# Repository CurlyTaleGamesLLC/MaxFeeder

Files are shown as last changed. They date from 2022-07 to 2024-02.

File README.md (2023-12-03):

# Max Feeder

<video autoplay loop muted src="https://user-images.githubusercontent.com/25337335/216802715-1deb94b0-7a2f-4627-93f5-1e41935b5955.mp4">
</video>

## Part Feeding Simplified
### Designed to automate feeding parts for your Open PnP compatible pick and place machine
<br/>

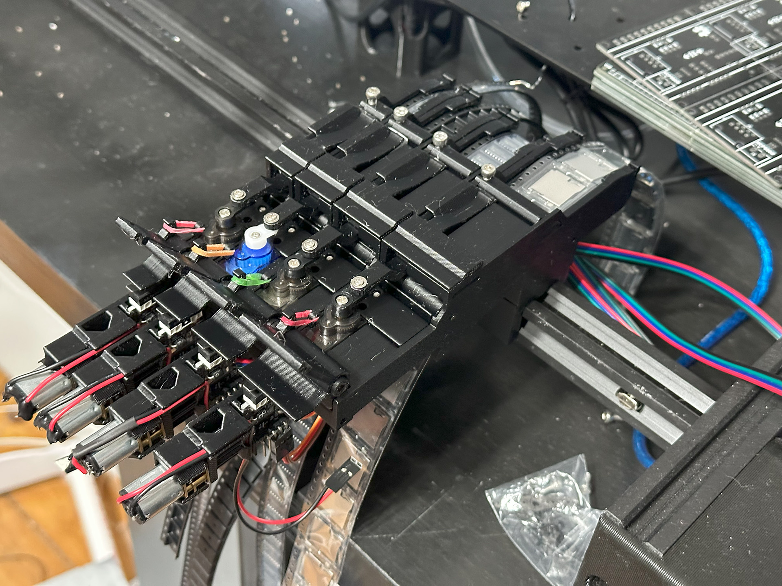
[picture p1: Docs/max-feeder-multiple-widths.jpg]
Max Feeders of multiple widths


This feeder is designed to be set up as an AutoFeeder in OpenPNP. It easily clips to 2020 aluminum extrusion and uses an Arduino Mega to receive Gcode commands sent over a USB serial connection in Open PnP. The Max Feeder Shield can control up to 34 feeders.

The design of the Max Feeder is based on [the 0816 feeder design from mgrl.](https://docs.mgrl.de/maschine:pickandplace:feeder:0816feeder) However after two years of development I redesigned every piece of it to improve and simplify the feeder as much as possible.

During development, I also referenced the remix of the 0816 feeder made Nicmoly for the Lumen PNP.

<br/>

# Where can I get a Max Feeder?

[I am selling kits of the Max Feeder Shield and kits of 5x 8mm Max Feeders.](https://store.curlytalegames.com/pages/max-feeders)
> The online store is now live! Thanks for supporting this open hardware project!

This is an Open Hardware project, so all of the design files and the BOM are included in this repo as well.

[If you like what I'm doing consider becoming a Github Sponsor :gift_heart:](https://github.com/sponsors/CurlyTaleGames)

<br/>

# Hardware

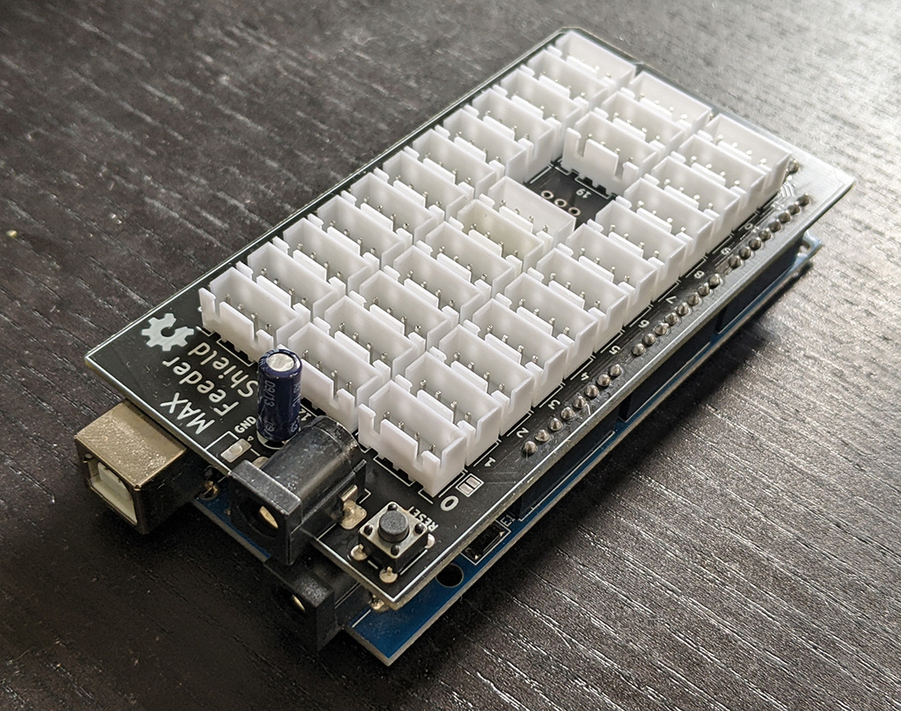
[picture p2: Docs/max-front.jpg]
Max Feeder Shield


## Max Feeder Shield
- 1 - Max Feeder Shield PCB
- 34 - 4 Pin 2.54mm JST connectors
- 1 - Arduino Mega
- 1 - 10uf Capacitor
- 1 - Barrel Jack
- 1 - 3.81mm Screw Terminal - Optional
- 1 - 6mm Through Hole Tacticle Switch
- 1 - 5v DC 3A (or more) Power Supply
- LOTS of 2.54mm Male Header
- Mounting Bracket in the "3D" folder

<br/>

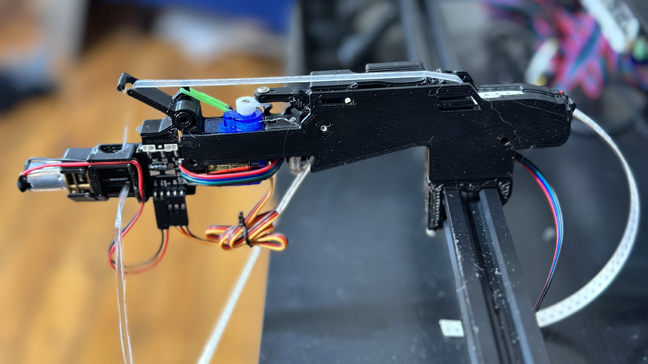
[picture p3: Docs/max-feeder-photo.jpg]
Max Feeder 8mm


## Max Feeder
- 1 - Max Feeder PCB
- 3D printed files in the "3D" folder
- 5 - [M3 6mm screws](https://www.amazon.com/Alloy-Steel-Socket-Screws-Black/dp/B00W8YSCIS/)
- 1 - [4 Pin 2.54mm JST cables 100cm in length ("stepper motor cable")](https://www.amazon.com/Wires-Motor-XH2-54-4P-PH2-0-6P-Printers-Accessories%EF%BC%8C3D/dp/B08PV6XGK2/)
- 3 - [M3 20mm screws](https://www.amazon.com/Prime-Line-9180478-Socket-Screws-10-Pack/dp/B07D5S3154/)
- 1 - [SPDT Limit Switch](https://www.amazon.com/dp/B088W8WMTB)
- 1 - [1N4001 Diode](https://www.amazon.com/MCIGICM-Rectifier-Electronic-Silicon-Doorbell/dp/B071YWNBVM/)
- 1 - [5 pin 2.54mm Angled Male Header](https://www.amazon.com/Antrader-2-54mm-Right-Header-Connector/dp/B07M88GRHG/)
- 1 - [2 pin 2.54mm Female header cable](https://www.amazon.com/Mayata-Female-Jumper-Dupont-Printer/dp/B07H1WDN3R/) or [Female to Female Dupont cables](https://www.amazon.com/EDGELEC-Breadboard-1pin-1pin-Connector-Multicolored/dp/B07GCZVCGS/)
- 1 - [N20 Geared DC Motor 60 RPM](https://www.aliexpress.com/item/3256803042731079.html?pdp_ext_f=%7B"sku_id":"12000024757391447"%7D)
- 1 - [MG90S Servo 180 degree](https://www.amazon.com/Compatible-Raspberry-Project-Helicopter-Airplane/dp/B0925V3X2S/)
- 1 - [M2 14mm dowel pin](https://www.amazon.com/MroMax-2-5x14mm-Stainless-Rust-Proof-Elements/dp/B07ZF4X7VQ/) or [2mm diameter rod cut to 14mm in length](https://www.amazon.com/dp/B0962RMLVJ)
- [Replacement Pen Springs](https://www.amazon.com/dp/B089JYV7BT)
- [Latex Free Orthodontic Elastics](https://www.amazon.com/dp/B08NCK1K6P)

<br/>

# 3D Prints

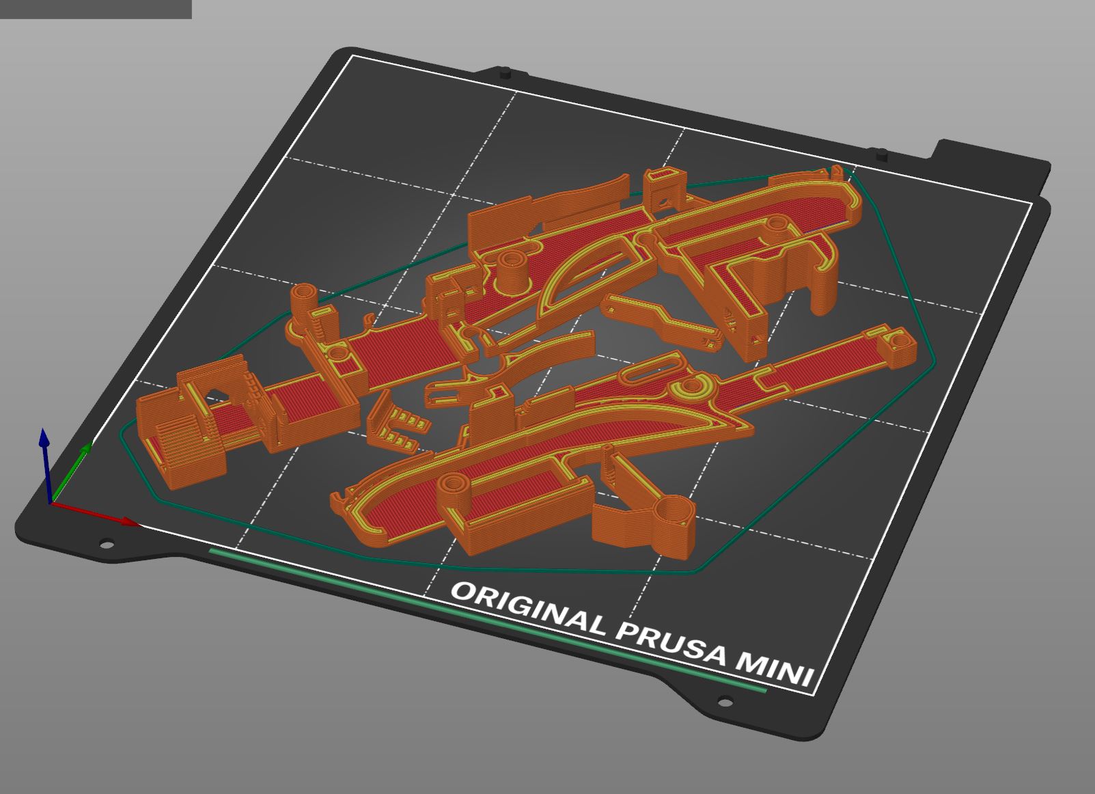
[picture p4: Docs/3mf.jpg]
Max Feeder Parts


## Max Feeder

Included are two 3MF files which has all the parts oriented and ready to print. Also there are the individual STL files if your slicer doesn't support 3MF files.

The files that need to be printed with a 0.4mm nozzle are labeled, all the other parts can be printed with 0.4mm, 0.6mm, or 0.8mm nozzles. Everything is designed to be printed without supports. If you print with a 0.8mm nozzle you can print a whole feeder in less than 1.5 hours.

[Download the 8mm Max Feeder.](/3D/8mm/) [12mm](/3D/12mm/), [16mm](/3D/16mm/), and [24mm](/3D/24mm/) versions are available in beta status. All of the feeder widths use the same hardware. The only difference between them are the 3D print files.

### Multiple Mounting Options

`FeederBase.stl` and `FeederCover.stl` are designed to clip onto 2020 aluminum extrusion. This is the default configuration of the Max Feeder and it's designed to mount to the Lumen PnP.

`DIN-FeederBase.stl` and `DIN-FeederCover.stl` are designed to clip onto DIN Rail for pick and place machines with a flat mounting surface, like the LitePlacer.

`2040-FeederBase.stl` and `2040-FeederCover.stl` are designed to clip onto 2040 aluminum extrusion. So it will mount to any pick and place machines that the original 0816 feeder can mount to.

<br/>

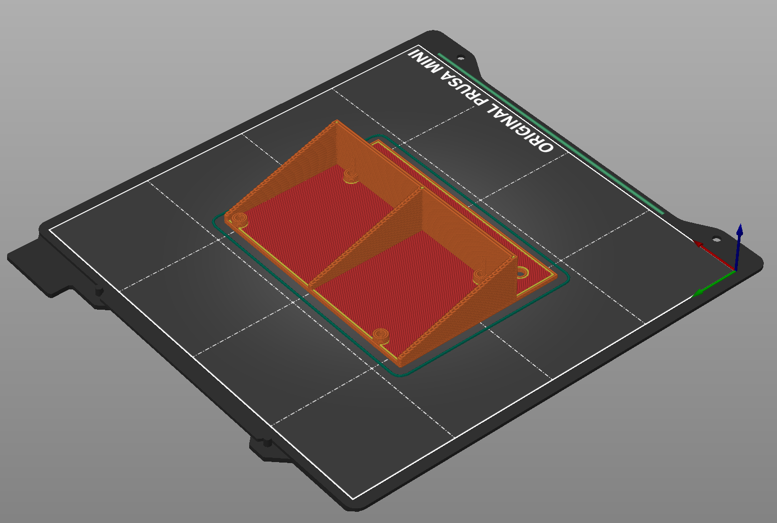
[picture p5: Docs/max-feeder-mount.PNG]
Max Feeder


## Max Feeder Shield

Included is a bracket to bolt a Max Feeder Shield + Arduino Mega compatible microcontroller to the side of some 2020 aluminum extrusion. The current bracket was designed to be used with a Lumen PNP but might work for other pick and place machines too.

[Download it here](/3D/Bracket/)

<br/>

# Feeder Assembly & Configuration

- [Uploading Firmware](./Docs/firmware.md)
- [Max Feeder PCB Assembly](./Docs/pcb.md)
- [Servo Poker Assembly](./Docs/poker.md)
- [Tape Gear Motor Assembly](./Docs/motor.md)
- [Final Feeder Assembly](./Docs/finishing-assembly.md)
- [Open PnP AutoFeeder Configuration](./Docs/openpnp.md)
- [Loading and Unloading Tape into Max Feeder](./Docs/finishing-assembly.md)

<br/>

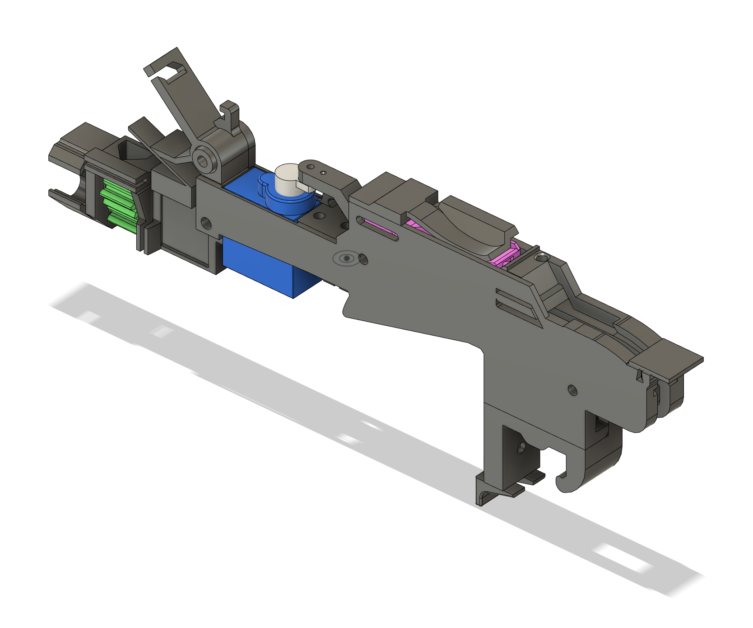
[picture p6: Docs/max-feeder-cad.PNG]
Max Feeder


## Reel Holder

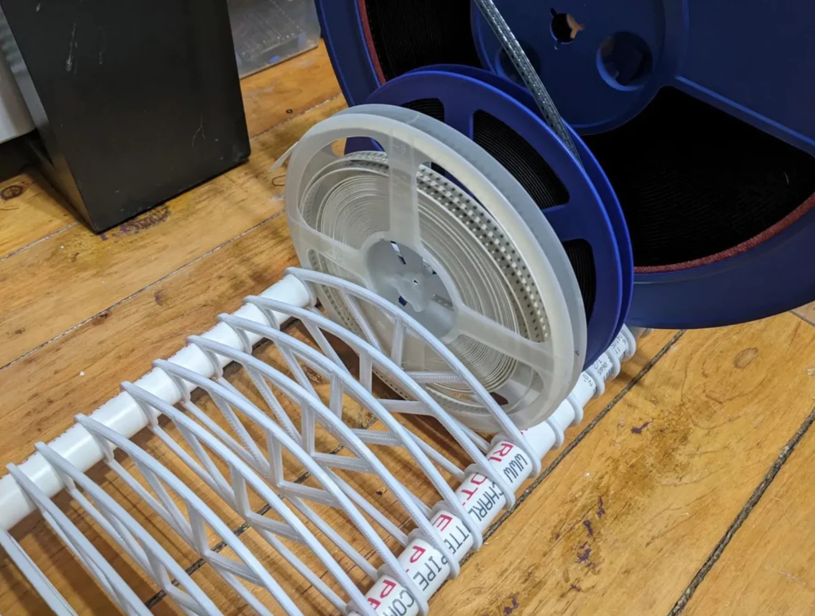
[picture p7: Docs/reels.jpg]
Reel holder


[Download and print this reel holder for your spools of parts](https://www.printables.com/model/343598-smd-reel-holder-for-pick-and-place-machine)

## Troubleshooting

If you are still having problems after going through the "Feeder Assembly & Configuration" [here are some solutions to common problems](./Docs/troubleshooting.md)

## Notes

There are a few optional parts for the feeder you can print.

### QR Code Cap

This part is attached to the front of your feeder and is designed to have a 1/2" x 1/2" QR code stuck onto it. [Atanisoft](https://github.com/atanisoft) and I have been working on [FeederUtils](https://github.com/atanisoft/FeederUtils), which features a way to import and automatically set up part feeders in Open PnP. The QR code portion of the project is still under development.

[Check it out here](https://github.com/atanisoft/FeederUtils)

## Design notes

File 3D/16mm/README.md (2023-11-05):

# 16mm Feeders are in Beta!

Feel free to try them out. The 16mm design has been working great, but needs more long term testing before they are out of beta. 

## Parts

The 16mm Max Feeders use exactly the same hardware as the 8mm kit which you can buy here:
[https://store.curlytalegames.com/pages/max-feeders](https://store.curlytalegames.com/pages/max-feeders)

## Setup

Follow the same instructions as the 8mm assembly and Open PnP configuration, however instead of feeding 4mm in Open PnP you'll want to feed 8mm.

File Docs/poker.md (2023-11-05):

# Max Feeder Servo Poker Assembly

You will need the following components to assemble the Servo Poker

- MG90S Servo
- MG90S Servo Horn
- MG90S Servo Screws
- Poker 3D print
- Poker Arm 3D print
- M3 6mm machine screw
- 2mm Smooth Rod - cut to 13mm in length
- Twist Tie

Note: the kits have been upgraded to use MG90S servos, however the documentation currently still shows SG90 servos. SG90 servos work reliably for 8mm and 12mm max feeders.

Don't want to source all these parts?
[Buy the kit!](https://store.curlytalegames.com/pages/max-feeders)

## Instructions

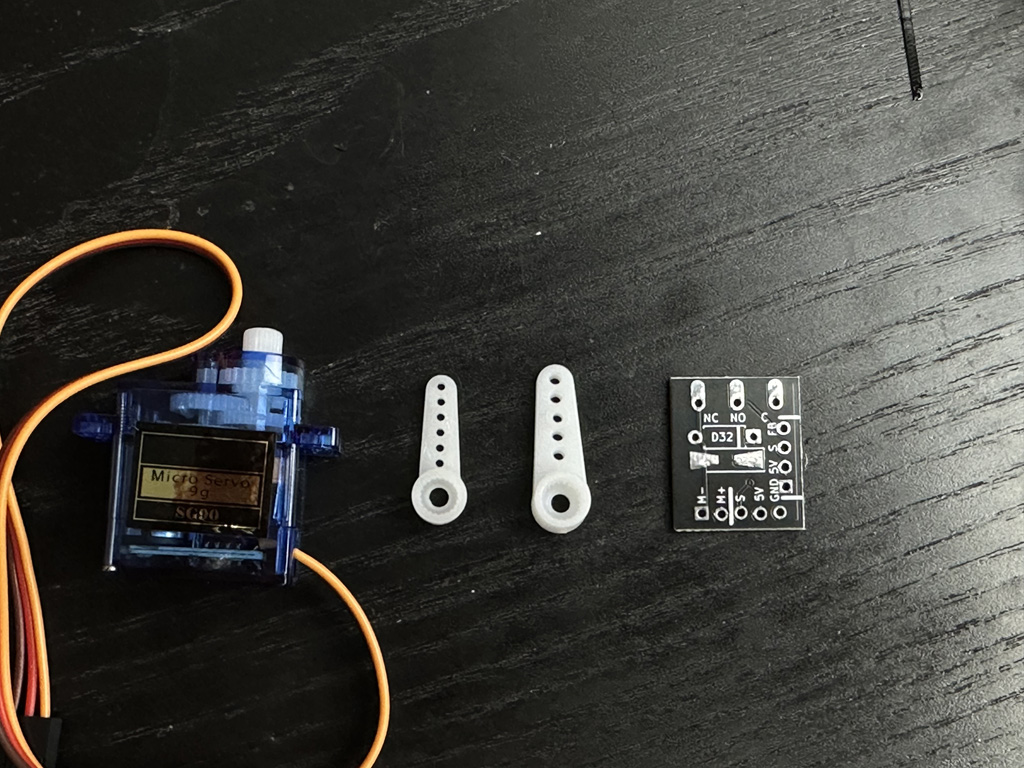
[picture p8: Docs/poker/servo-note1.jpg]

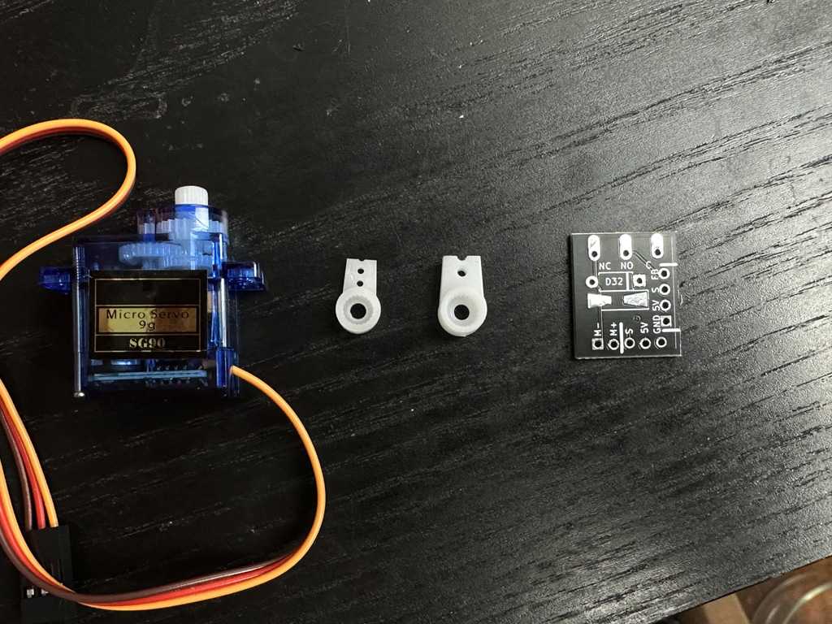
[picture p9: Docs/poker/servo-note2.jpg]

Locate the servo horn and depending on the size of the servo horn cut it at either the 2nd or 3rd hole. It should be roughly 6mm from center of the servo screw and the center of the hole you will attach the poker arm to. See above photo.

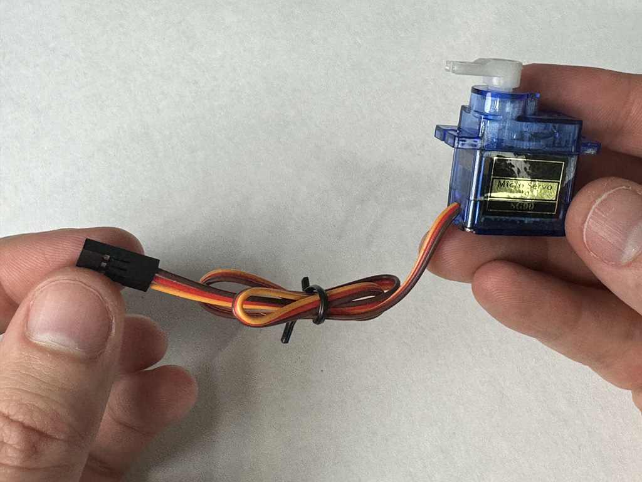
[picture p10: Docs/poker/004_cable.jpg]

Wrap the servo cable back and forth and use a twist tie to hold it in place.

## Poker Tip

### PCB Tips

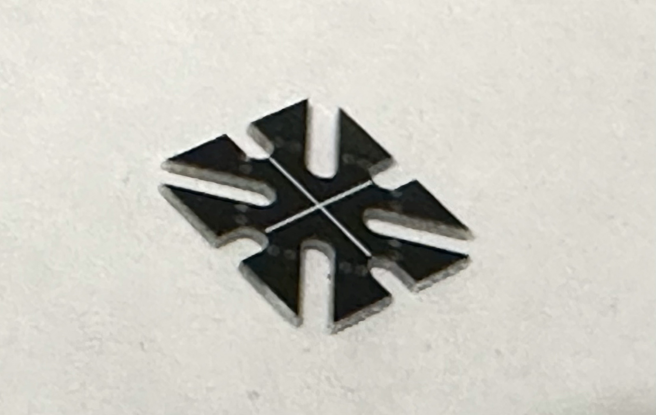
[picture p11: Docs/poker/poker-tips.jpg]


For new builds, snap off a tiny 0.8mm poker tip PCB, and push it onto the poker. The 3D print has a small clip that should hold it in place. Use some Super Glue (CA glue) to secure the PCB to the 3D print. 

If you didn't buy the kit and have some scrap 0.8mm PCBs lying around you can cut them into tiny triangles and glue those in place.

### Legacy Plastic Tip

Skip this step if you are using the new PCB poker tips (highly recommended).

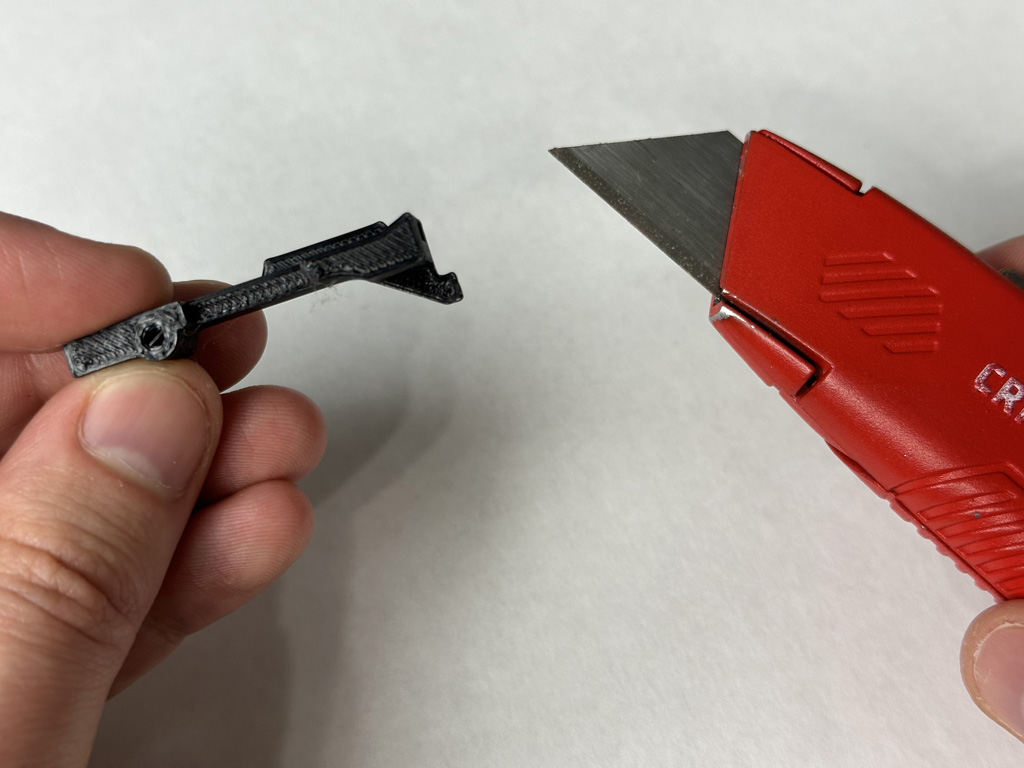
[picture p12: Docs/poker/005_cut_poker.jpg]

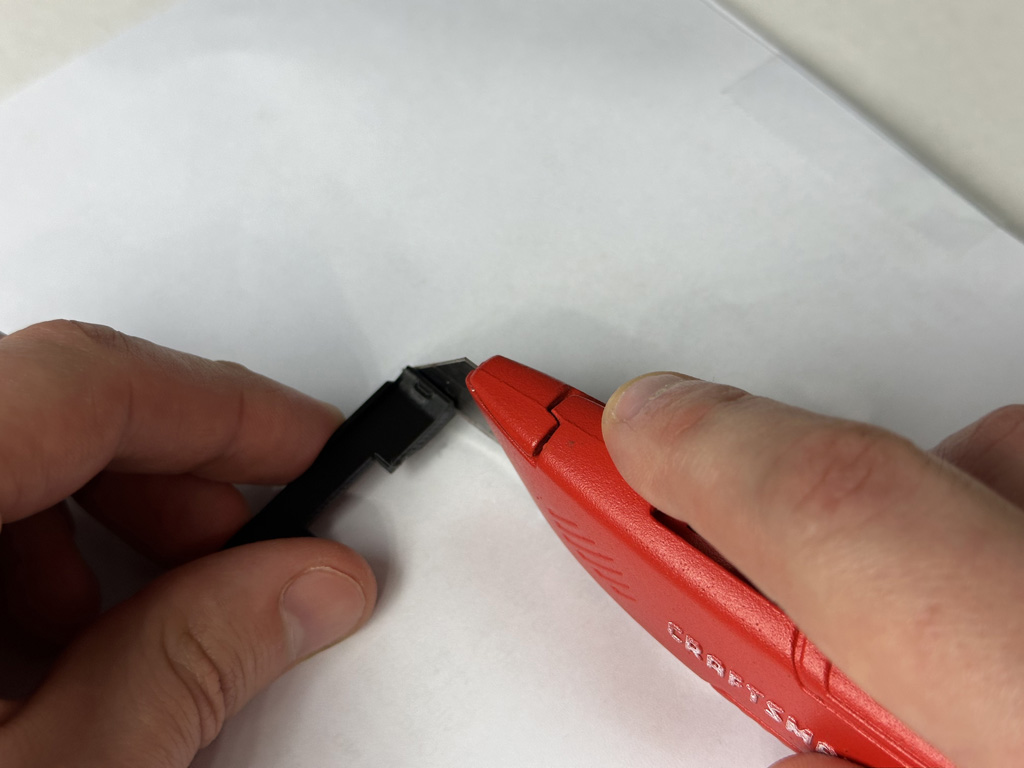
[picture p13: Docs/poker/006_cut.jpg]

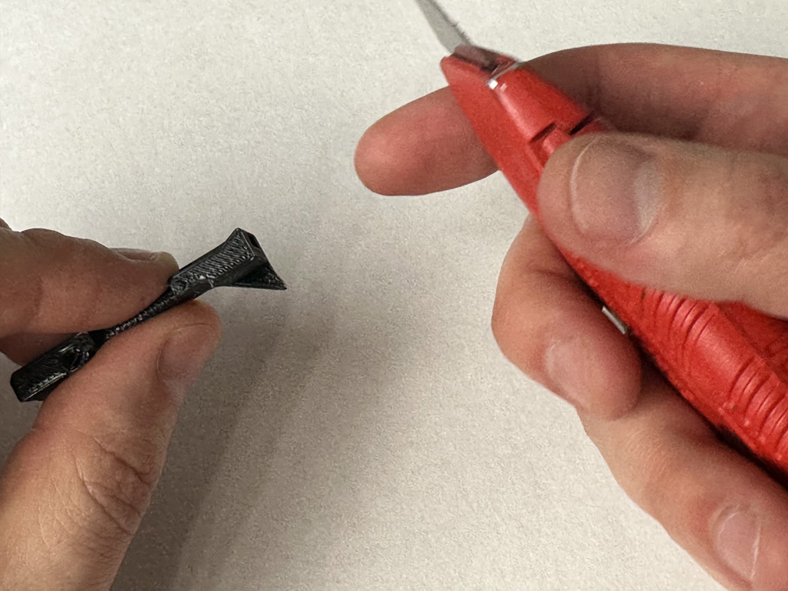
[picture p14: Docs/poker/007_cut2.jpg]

**Using a fresh blade on a box knife cut the tip of the poker. It's very important to keep the tip of the poker nice and pointy. That point will ratchet over the sprocket holes in the tape when the arm pulls back, and then it will catch in the holes when it moves forward.**

If it's too blunt or if you cut too much off it won't catch the sprocket holes on the 8mm SMD part tape. Don't try to cut it it with a dull blade, you won't get a sharp point and will regret it later.

## Adding Guide Pin

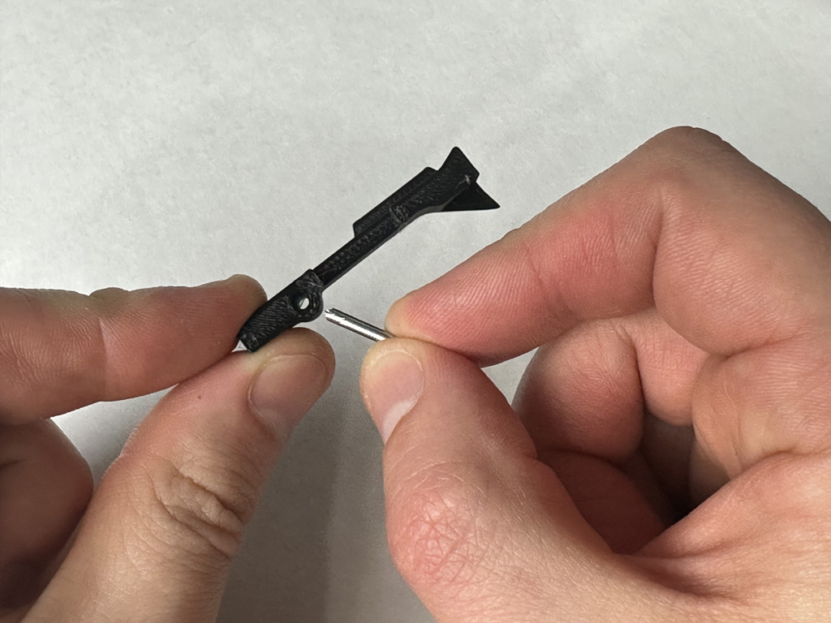
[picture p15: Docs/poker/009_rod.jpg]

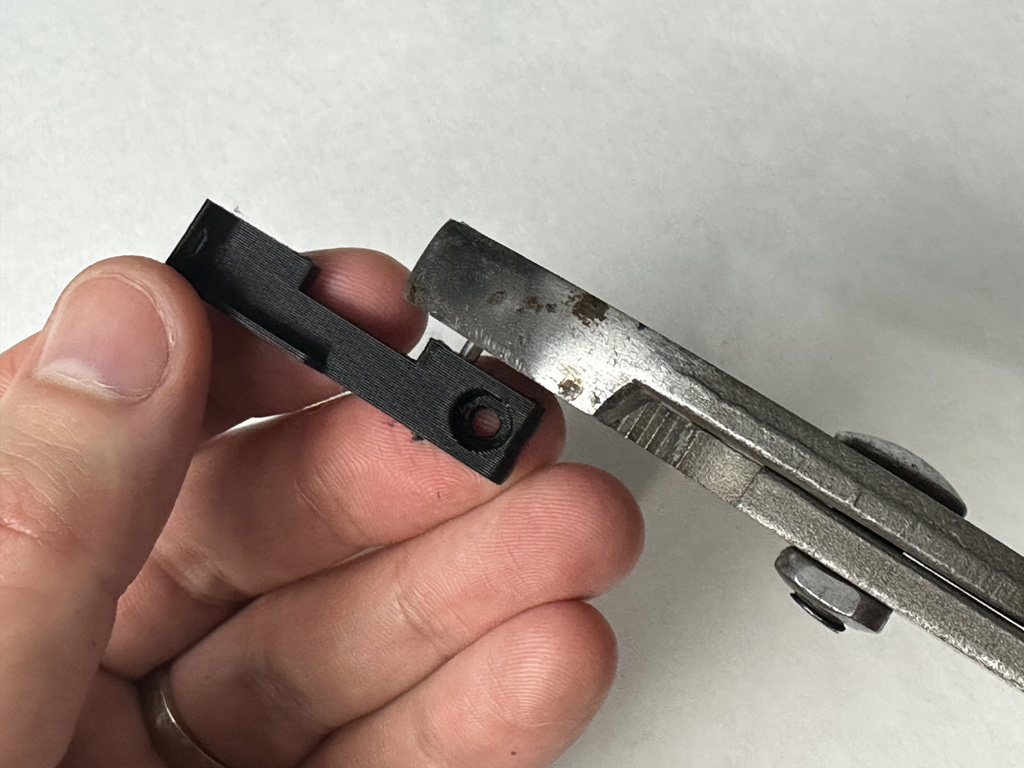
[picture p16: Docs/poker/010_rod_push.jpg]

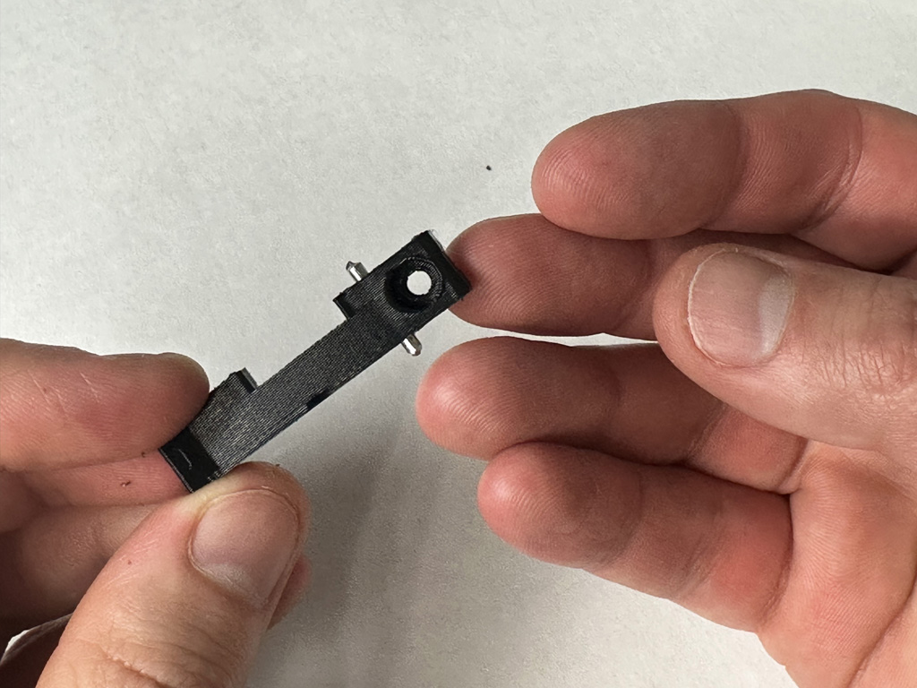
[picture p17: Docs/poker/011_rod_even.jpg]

Using some pliers push the 2mm smooth rod into the poker arm. It is a very tight fit and you will have to work the pliers back and forth to get the rod through. Make sure the rod is centered so the tips that are poking out are even on both sides.

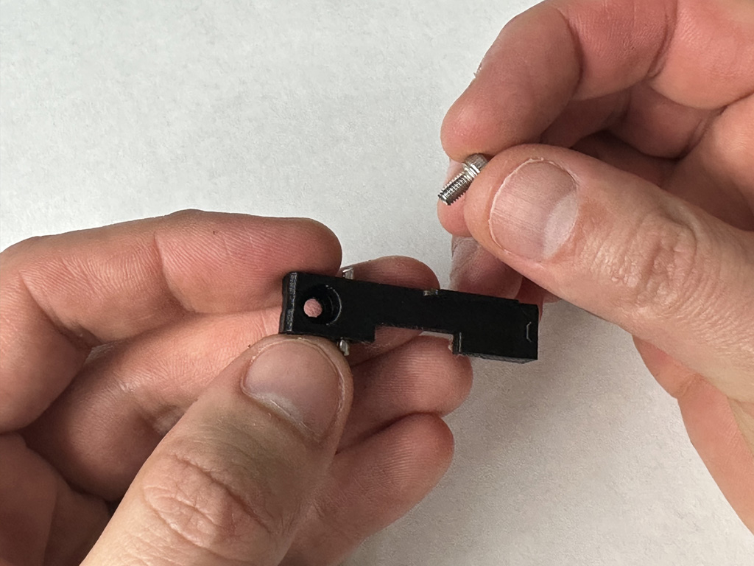
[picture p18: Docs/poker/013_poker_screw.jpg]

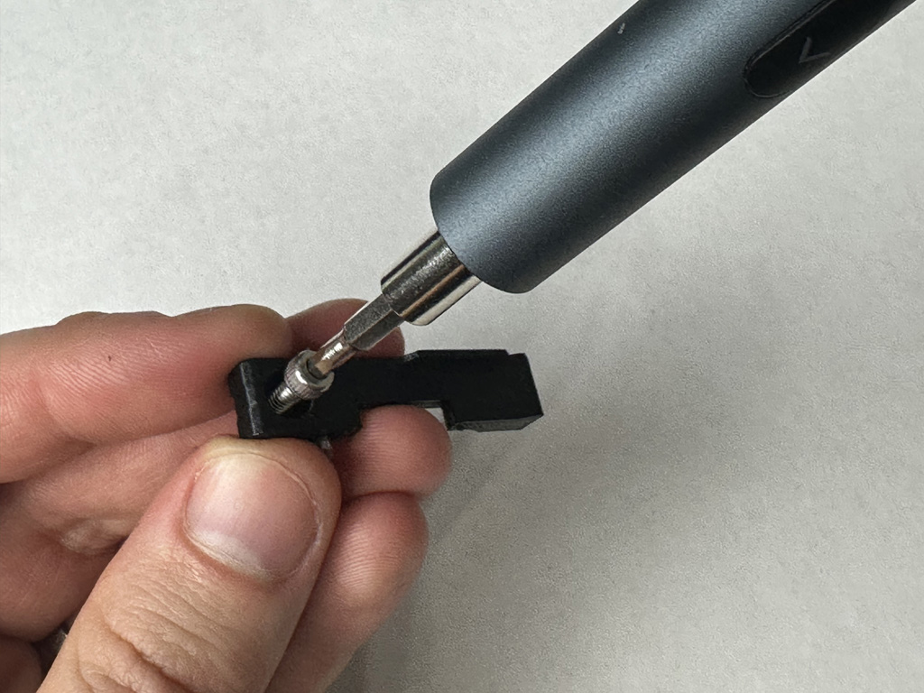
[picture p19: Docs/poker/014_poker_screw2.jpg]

Take a M3 6mm screw and screw it all the way through the hole on the poker.

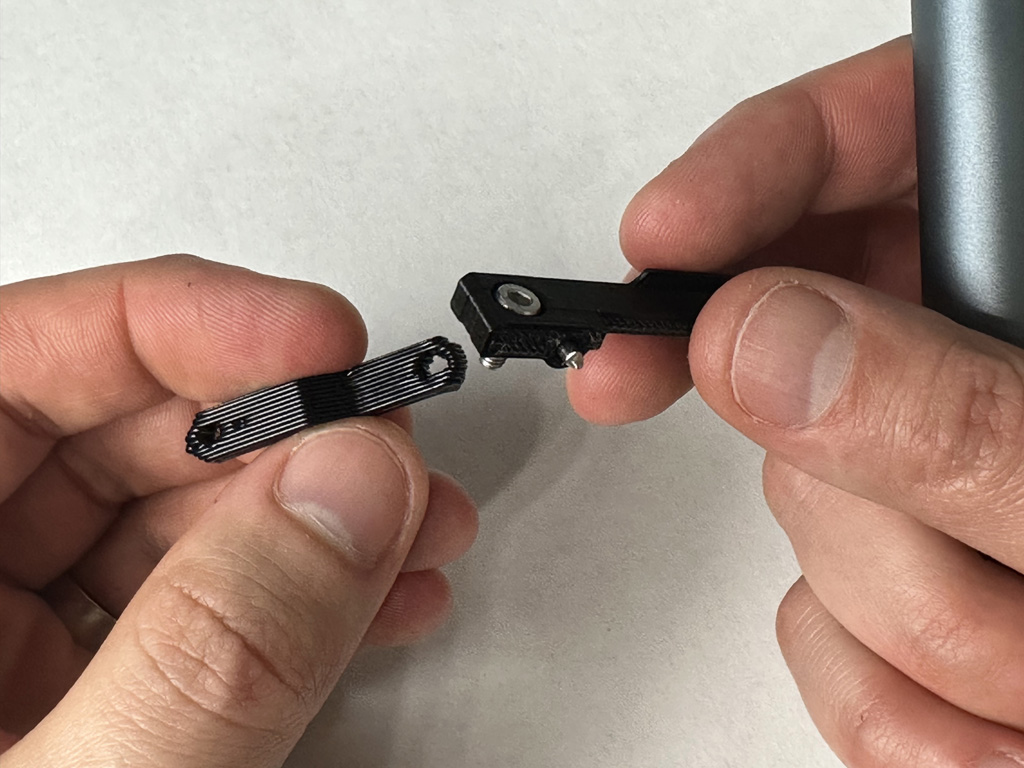
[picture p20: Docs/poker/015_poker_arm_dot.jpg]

The poker arm 3D print has two holes. There is a small dot to the right of the small hole. Orient the parts as shown and screw the M6 6mm screw into the larger hole on the poker arm.

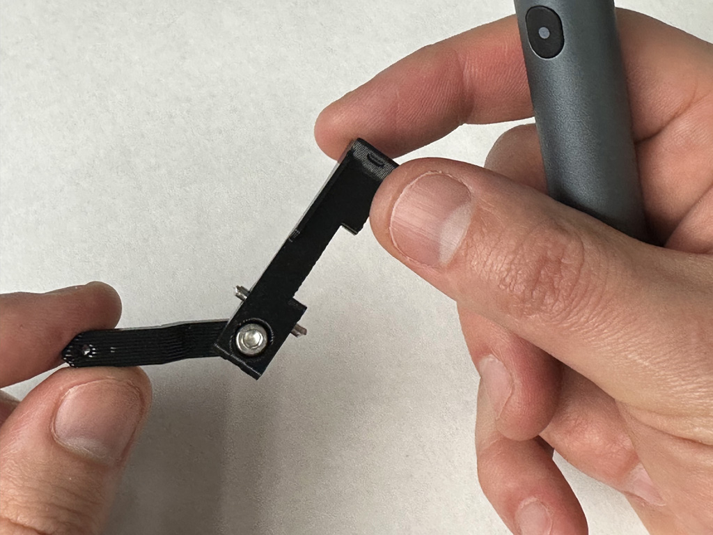
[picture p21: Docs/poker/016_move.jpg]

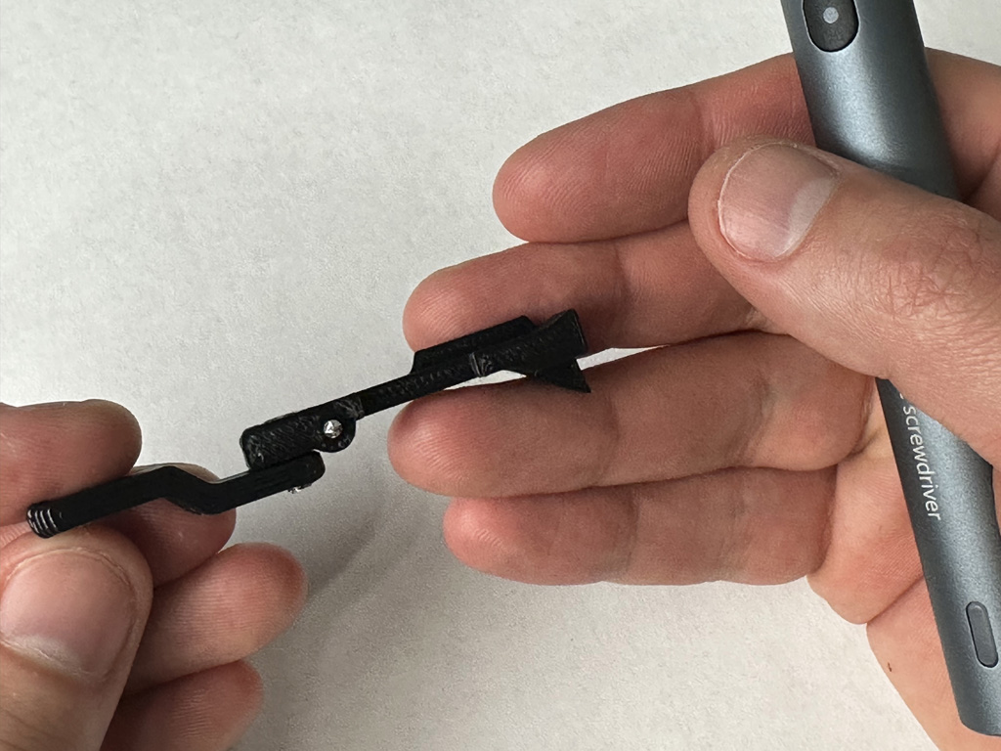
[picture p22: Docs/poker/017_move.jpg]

The screw should be tight but the poker and poker arm should be able to pivot on the M3 6mm screw.

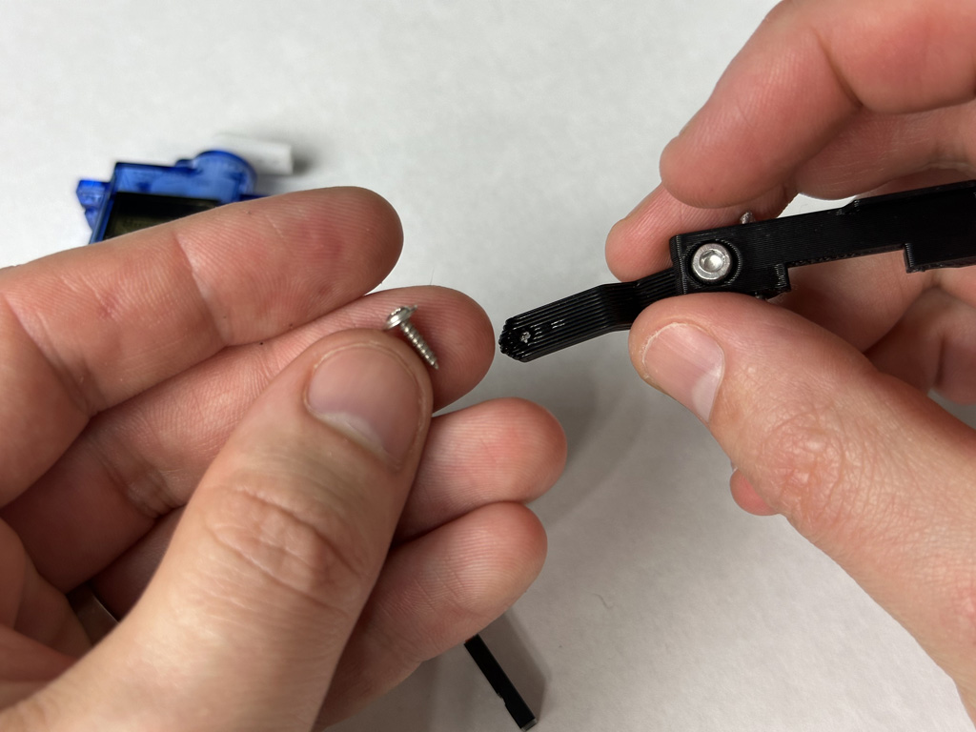
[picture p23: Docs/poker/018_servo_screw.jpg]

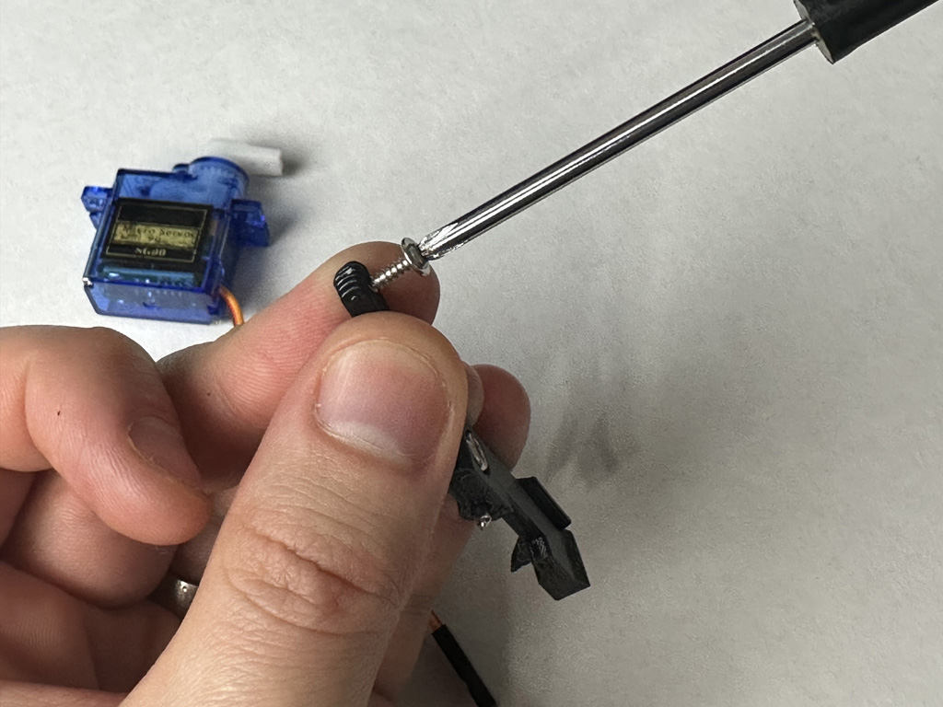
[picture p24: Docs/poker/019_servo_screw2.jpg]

Take one of the servo horn screws and screw it into small hole on the poker arm. The hole is tight to prevent slop when the servo advances the tape later, however you still want the 3D print to rotate freely. Widen the hole slightly by screwing and unscrewing the servo horn screw in the 3D print.

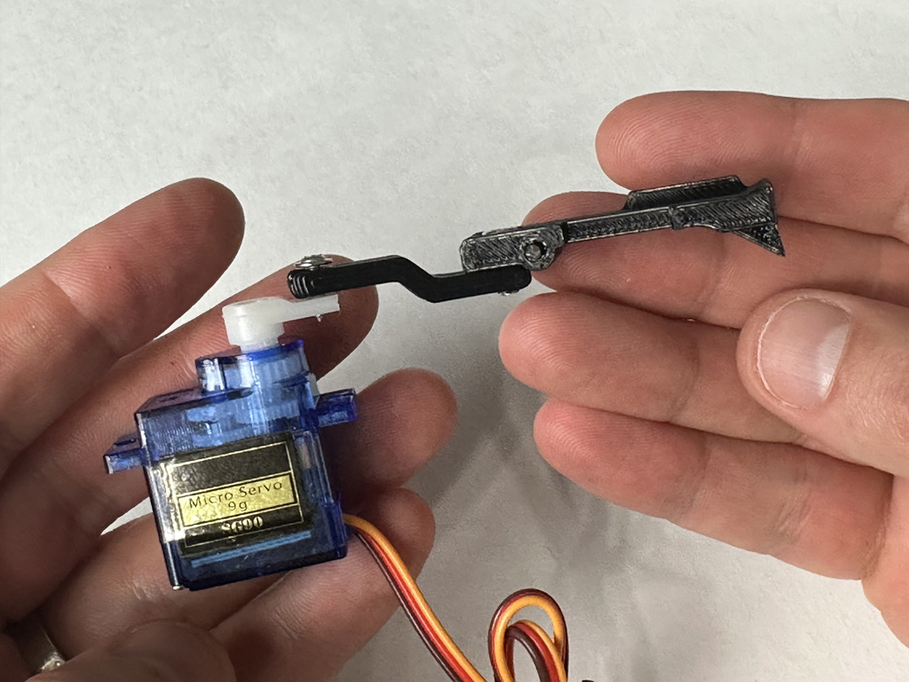
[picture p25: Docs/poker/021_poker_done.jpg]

Attach the poker arm to the servo horn using the servo horn screw. Screw into the last hole on the cut servo horn.

### [Next Step: Tape Gear Motor Assembly](motor.md)

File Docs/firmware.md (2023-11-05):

# Max Feeder Shield Firmware

To use the Max Feeder Shield you'll need to upload the latest firmware onto an Arduino Mega. 

If you purchased the Max Feeder Shield + Microcontroller from [store.curlytalegames.com](https://store.curlytalegames.com/pages/max-feeders) you can skip this, it comes pre-loaded with the latest firmware. 
> The online store is now live! Thanks for supporting this open hardware project!

I have included a modified version the 0816 feeder firmware originally written by mgrl in this repository. I added support for things like Software Servo control, and auto detaching for servos so they don't burn themselves out.

[You can find it located here.](/Firmware/0816feeder/)

<br/>

## Installation

To flash the firmware onto an Arduino Mega you'll need to install the [Arduino IDE](https://www.arduino.cc/en/software)

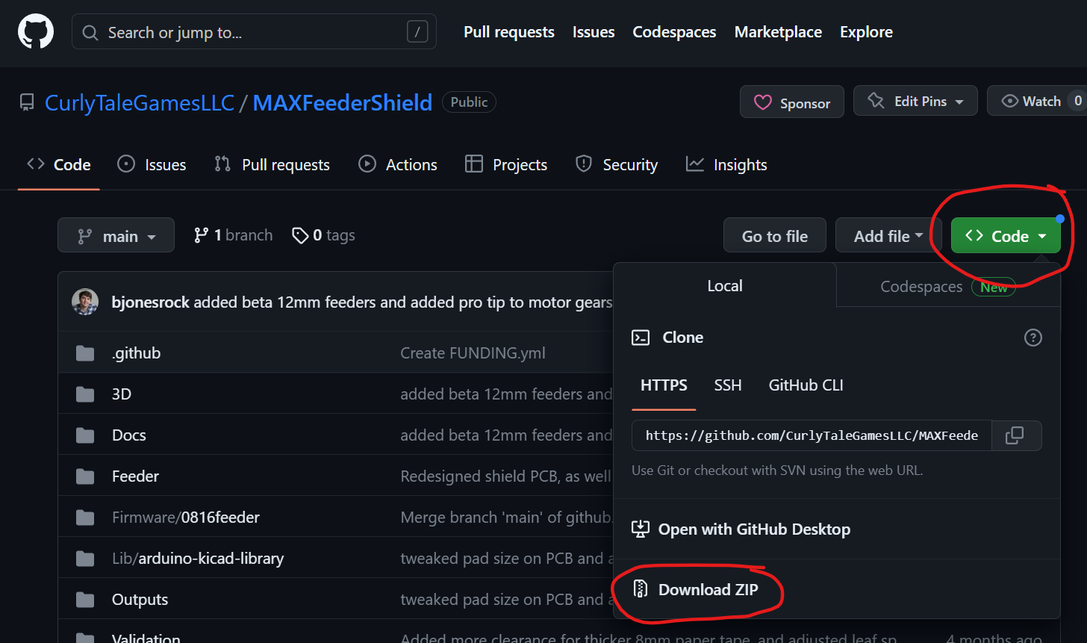
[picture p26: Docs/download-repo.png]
Download Files


Download a copy of this Github Repo

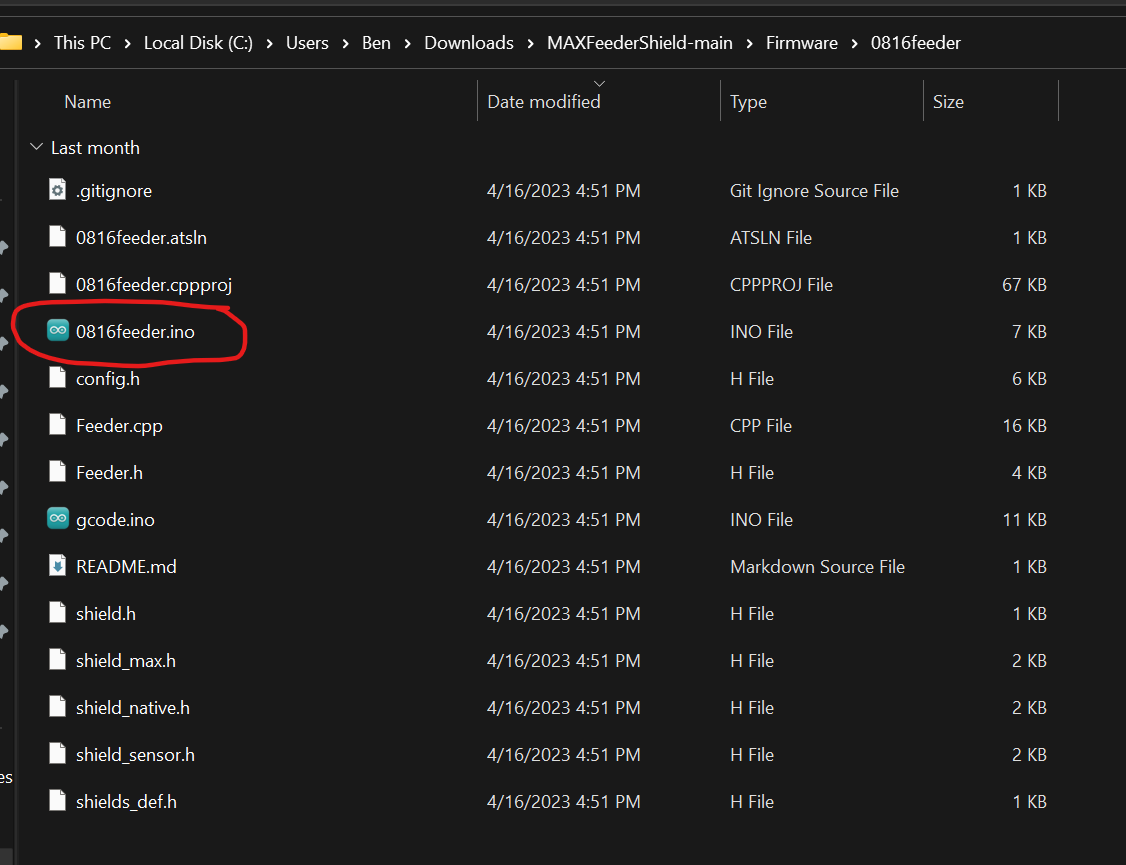
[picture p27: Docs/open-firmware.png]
Open Arduino Firmware


Open the **"0816feeder.ino"** inside the [**"Firmware > 0816feeder"** folder](/Firmware/0816feeder/)

Go to **"Tools > Manage Libraries"**

Search for **"EEPROMex"** and install the latest version

Search for **"SoftServo" by AlexGyver** and install the latest version

Connect to the Arduino Mega over serial by going to **"Tools > Port > COMx"** if you're on a Mac or Linux computer it will display the serial port as "/dev/xxxx"

**Press the Upload button** to write the firmware to the Arduino Mega

<br/>

### [Next Step: Max Feeder PCB Assembly](pcb.md)

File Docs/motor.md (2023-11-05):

# Max Feeder Tape Gear Motor Assembly

You will need the following components to assemble the Tape Gear Motor

- N20 Geared DC motor
- M3 20mm machine screw
- 2 Pin 2.54mm cable (cut in half)
- FeederBase 3D Print
- 1mm-20deg-8t-key-axel-0.4mm-nozzle 3D Print
- 1mm-20deg-7t-m3-0.4mm-nozzle 3D Print

Don't want to source all these parts?
[Buy the kit!](https://store.curlytalegames.com/pages/max-feeders)

Note: There are multiple 3D print files included in this repo to account for tolerances of different 3D printers. Print a couple and see which fits the shaft of the motor and M3 20mm screw best for you.

## Instructions

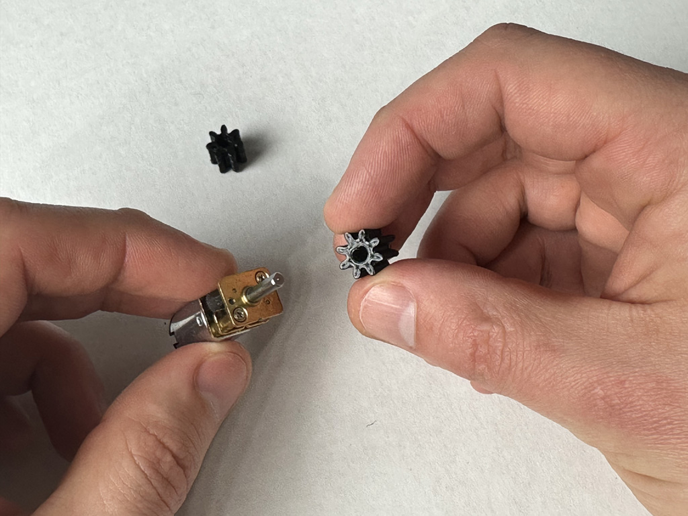
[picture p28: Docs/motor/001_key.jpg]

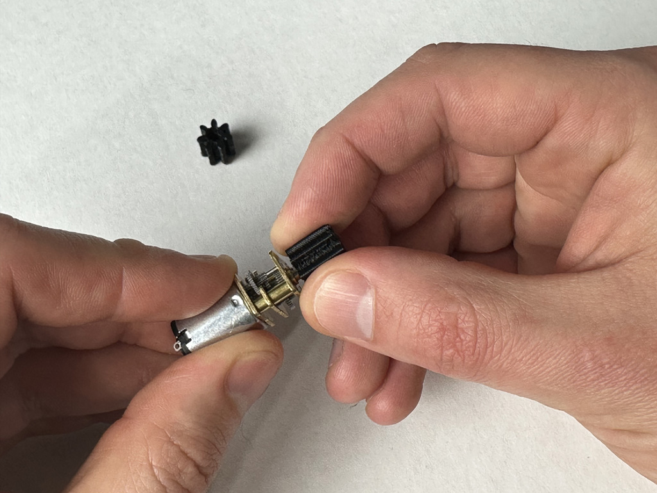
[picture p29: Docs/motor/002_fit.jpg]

Take the N20 motor and push it in and pull it out of the keyed 8 tooth gear several times. We want to loosen the hole a little.

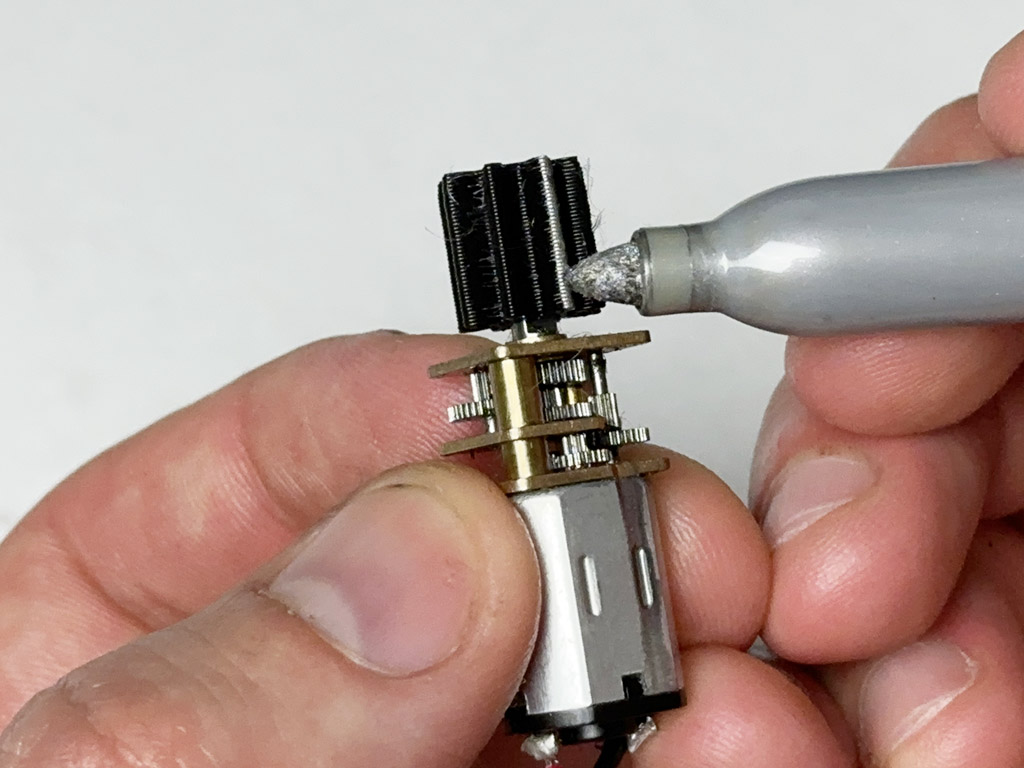
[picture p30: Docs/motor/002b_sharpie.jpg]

**Pro Tip! Mark the keyed 8 tooth gear with marker to help with lining up the key in the motor shaft.**

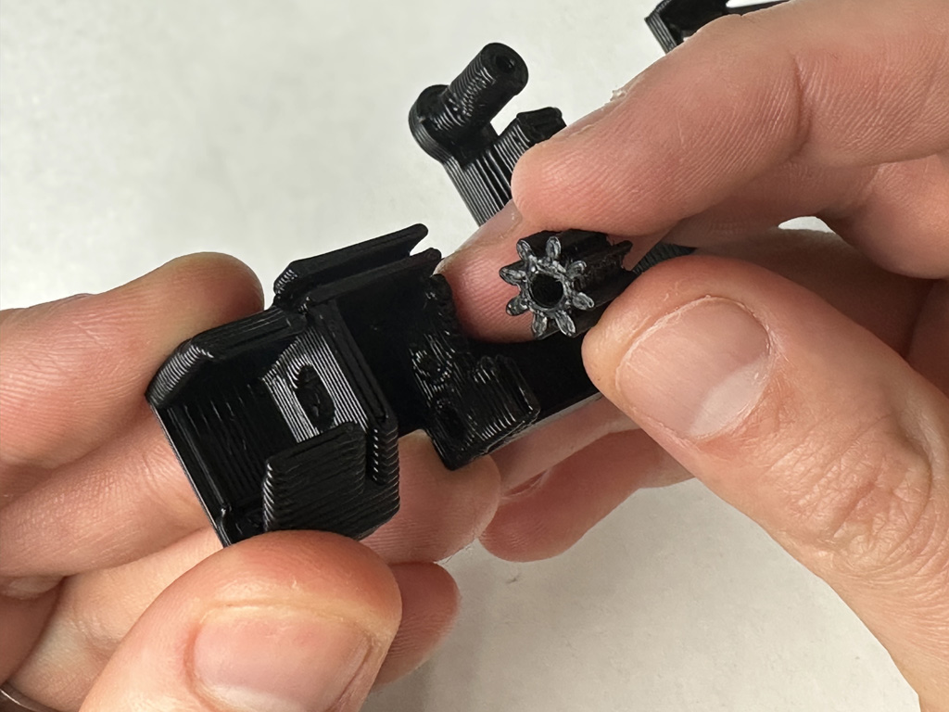
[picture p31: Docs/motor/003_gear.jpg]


Insert the 8 tooth gear into the housing. The keyed side of the gear should face the left side, and the round side of the gear should fit onto the small bump on the right side of the housing. Bend the housing slightly so the gear will drop into place.


Spin the gear to line up the key in the gear with the keyed motor shaft. Press the motor into place, it may take a few attempts and some wiggling to get it to fit.




Push the N20 motor all the way in




Screw the M3 20mm screw into the hole below the motor. Stop when you see the tip of it coming out of the 3D print.


Slide the 7 tooth gear into place.


Screw the M3 20mm screw all the way in. Then back it out slightly so the gear isn't being squeezed. 

If you find that your tape isn't catching in the gears later you might need to tighten this screw more.



Cut the 2 Pin 2.54mm cable in half, and strip about 2-3mm of insulation off the ends.


Poke the wires through the holes on the contacts of the motor, making sure to match the Red wire with the + side of the motor.


Solder the wires to the motor

Pro tip: after soldering, add a small dot of hot glue to secure the soldered wires to the motor housing. This will prevent the wires from being ripped off accidentally. If they get ripped off, don't worry it's easy enough to resolder them.



Push the motor wires into the strain relief as shown above.

### [Next Step: Finishing Assembling the Max Feeder](finishing-assembly.md)

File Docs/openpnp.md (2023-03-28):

# Max Feeder Open PnP AutoFeeder Configuration

You will need at least 1 Max Feeder, and Max Feeder Shield assembled and connected to your computer. As well as Open PnP installed and your pick and place machine configured.

Need the parts to assemble some Max Feeders? [Buy the kit!](https://store.curlytalegames.com/pages/max-feeders)

## Instructions



Go to the Machine Setup tab select Drivers and click the + button to add a new Driver.



Select GcodeDriver and click Accept



Rename the driver to MaxFeeder, set the communications type to serial

Select the COM port of the Max Feeder, and set the baud rate and other serial settings to match the screenshot above.

Click Apply.



Each feeder is set up as an Actuator in Open PnP. Select "Actuators" from the Machine Setup window, and then click the + button to add a new Actuator.



Select ReferenceActuator, and then click Accept.



Set the Driver of the new Actuator to use the MaxFeeder GcodeDriver. Name the Actuator N0 for feeder index 0. Increment this value up for each feeder you create.

In the "General" actuator settings set the Value Type to "Double", and the "ON Value" to 4.0

This is the amount of mm you want the feeder to advance based on the size of your part. For 8mm tape you typically want this to be 4mm.

Set the Enabled state to LeaveAsIs

Set the Index to match the index of the feeder. So if this is the first feeder you'd set it to 0.

Click Apply.



Select the MaxFeeder Gcode Driver and go to the Gcode tab.

Select Default, and then under Setting select `COMMAND_CONFIRM_REGEX`

Copy and paste this Regex:
```
^ok.*
```
Click Apply

This reads the confirmation gcode that the Arduino Mega will send back when it completes a command.



Select `COMMAND_ERROR_REGEX` and copy and paste in this Regex:
```
^error.*
```

Click Apply



Now let's set up the Gcode for a feeder.

Select the actuator you just created, this one is called N0



Select `ACTUATE_DOUBLE_COMMAND` in the Setting dropdown



Enter this Regex:
```
M600 N{Index} F{DoubleValue}
```

Click Apply

You will use the same regex for all of your Max Feeders/Actuators in Open PnP.

Here is an explaination of what each part of the command is.

| Gcode  | Meaning |
| --- | --- |
| `M600`  | Move command for the servo  |
| `N{Index}`  | index of the feeder you want to move. The `{Index}` will use the index you set in the Actuator  |
| `F{DoubleValue}`  | The distance in mm to move the tape forward, it gets this value from the `Double value` you set in the feeder later |

For our feeder the final Gcode that gets sent would be:
```
M600 N0 F4
```

## Creating the AutoFeeders



In the `Feeders` tab, click the + button to add a new feeder.



Select ReferenceAutoFeeder, and click Accept.



Select the part you want to assign to the feeder.

Move the tip of the pick and place nozzle directly on top of the first fully exposed part on the Max Feeder. Click the Capture Tool Position button to get the position of the part on your pick and place machine.

Set the Actuator to use `N0`, the name of the actuator that is controlling that feeder.

Set the Actuator Value to 4. Most 8mm tape parts use a feeding distance of 4mm, but if the part you are feeding requires something else you can enter that there.

Click the Apply button.

Once the tape is loaded you can test feeding parts by pressing the `Test feed` button.

## [Next Step: Loading and Unloading Tape](tape.md)

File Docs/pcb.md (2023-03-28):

# Max Feeder PCB Assembly

You will need the following components to assemble the Max Feeder PCB

- Max Feeder PCB
- SPDT Microswitch
- Diode
- 5 pin 2.54mm Angled Male Header
- 4 Pin JST cable ("Stepper Motor" Cable)

Don't want to source all these parts?
[Buy the kit!](https://store.curlytalegames.com/pages/max-feeders)
## Instructions

Cut off the 6 pin end from the 4 pin JST cable
Cut off the 6 pin end from the 4 pin JST cable

Strip a few millimeters of insulation off the wires
Strip a few millimeters of insulation off the wires

Max Feeder PCB Strip
The Max Feeder PCBs are V-cut into strips

Snap off a PCB
Snap off a single Max Feeder PCB

Take a diode
Grab a diode

Insert the diode into the PCB
Insert the diode into the PCB as shown

Grab some angled header
Grab a 5 pin 2.54mm angled header

Insert the angled header as shown
Insert the angled header as shown

Grab a SPDT microswitch
Grab a SPDT microswitch

Line up the switch with the pads as shown
Line up the switch with the pads as shown

Soldered, front of PCB
Soldered, back of PCB
Solder the diode, switch, header, and cable to the PCB

Repeat these steps to assemble all of your Max Feeder PCBs.

### [Next Step: Servo Poker Assembly](poker.md)

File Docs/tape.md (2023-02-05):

# Max Feeder Loading Tape

<video src="https://user-images.githubusercontent.com/25337335/216800410-1600b681-8f9a-426c-9a17-0ce485b8a45b.mp4" data-canonical-src="https://user-images.githubusercontent.com/25337335/216800410-1600b681-8f9a-426c-9a17-0ce485b8a45b.mp4" controls="controls" muted="muted" class="d-block rounded-bottom-2 border-top width-fit" style="max-height:640px; min-height: 200px">
</video>

To load tape insert the tape in front of the spring screw on the bottom. You can double click the tape lever to actuate the servo to help feed the tape through.

If you find the servo is pusing the tape backwards tighten down the screw on the top of the Max Feeder to add a little more friction so the servo can ratchet the poker arm back without moving the tape.

Once some of the tape is poking out of the front of the feeder you can pull it through manually.

Peel the cover tape back and thread it through the hole in the tape lever. Then push the tape into the spinning gears of the tape motor. When the gears catch the tape it will pull the lever down pressing the switch on the feeder causing it to turn the motor off.

When the feeder actuates the tape will have some slack which will cause the lever to lift up and turn the motor back on which will then pull the slack below until it causes the lever to be pulled down again and turn off the motor again.

# Max Feeder Unloading Tape

<video src="https://user-images.githubusercontent.com/25337335/216800415-54cb2c33-2e54-47c1-9b32-2b51a95d75dc.mp4" data-canonical-src="https://user-images.githubusercontent.com/25337335/216800415-54cb2c33-2e54-47c1-9b32-2b51a95d75dc.mp4" controls="controls" muted="muted" class="d-block rounded-bottom-2 border-top width-fit" style="max-height:640px; min-height: 200px">
</video>

There is a small slot on the front of the poker arm. If you stick a small flat head screw driver, or some tweezers into that slot and pry it up the poker arm will no longer touch the sprocket holes on the tape allowing you to pull the tape out of the feeder.

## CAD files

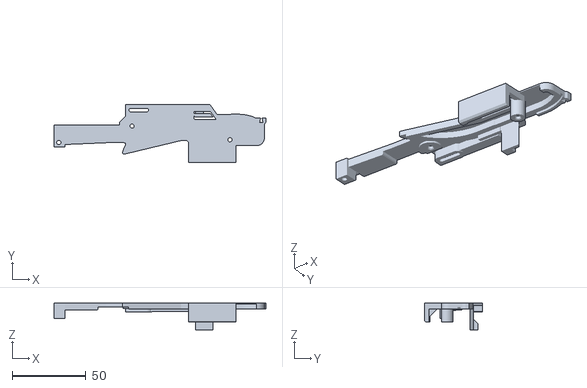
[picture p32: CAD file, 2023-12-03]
3D/12mm/FeederCover.stl
143.3 x 39.5 x 17.9

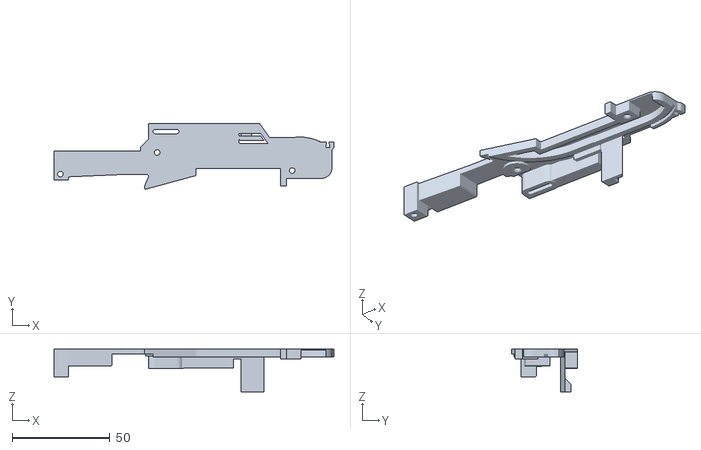
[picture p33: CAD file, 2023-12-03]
3D/16mm/2040-FeederCover.stl
143.3 x 33.6 x 21.9

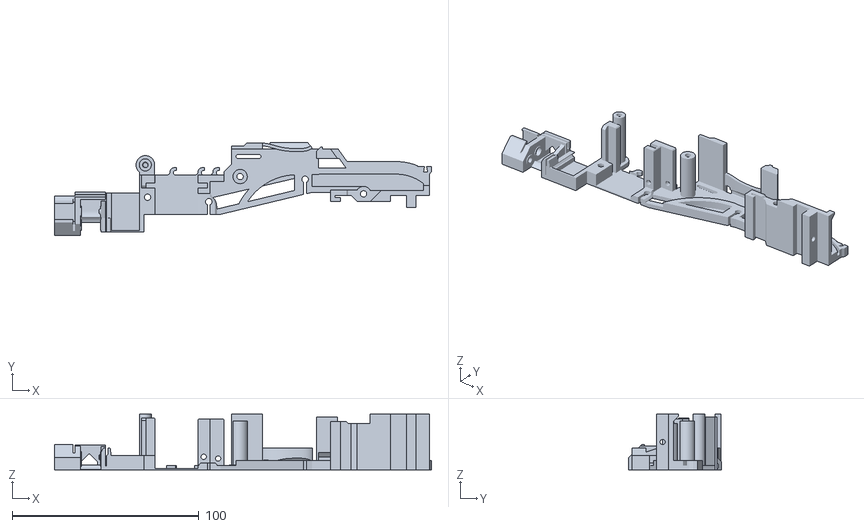
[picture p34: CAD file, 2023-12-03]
3D/24mm/DIN-FeederBase.stl
201.9 x 50.0 x 29.9

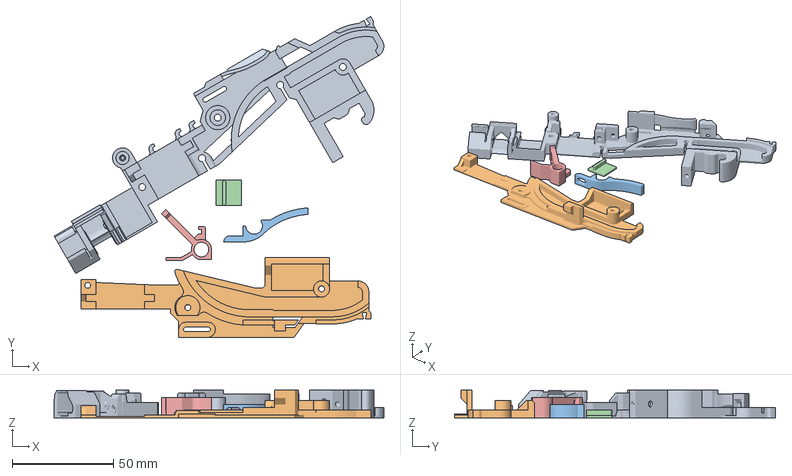
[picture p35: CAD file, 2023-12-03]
3D/8mm/_max-feeder-8mm-plate.3mf
163.1 x 158.8 x 13.7 mm
FeederBase.stl
FeederCover.stl
PressureArm.stl
QRCap-optional.stl
TapeLever.stl

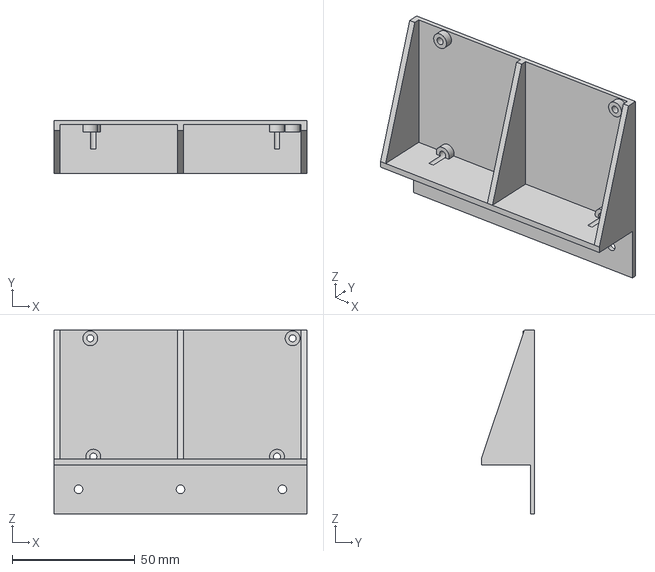
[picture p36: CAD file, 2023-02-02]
3D/Bracket/MaxFeederShieldMount.step
103.2 x 21.8 x 74.9 mm

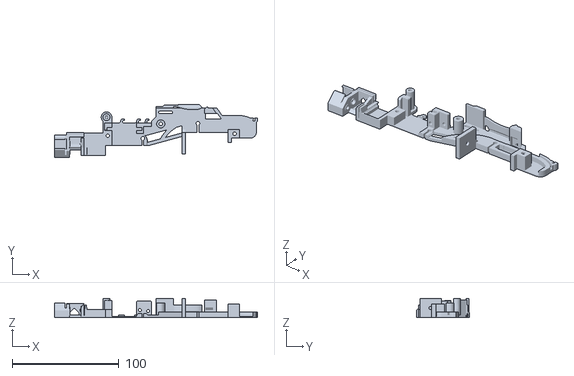
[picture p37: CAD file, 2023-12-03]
3D/12mm/2040-FeederBase.stl
189.9 x 50.0 x 17.9

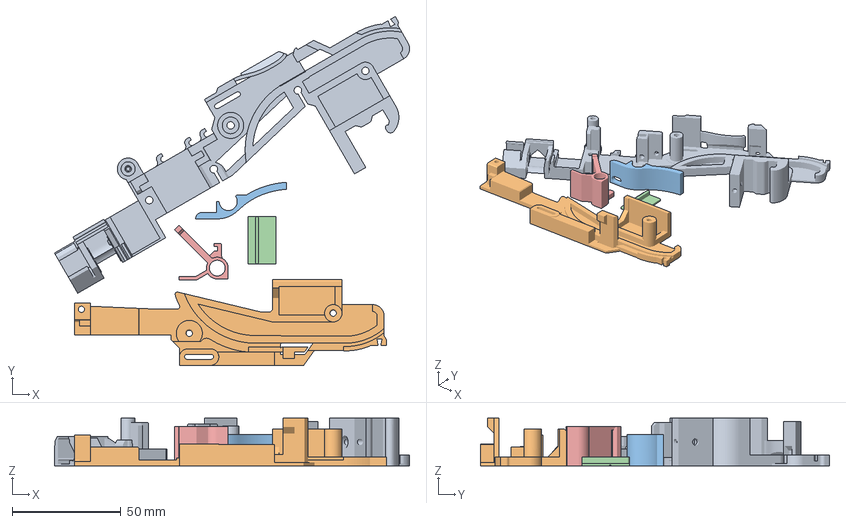
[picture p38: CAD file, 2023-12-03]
3D/16mm/_max-feeder-16mm-plate.3mf
163.1 x 160.3 x 21.9 mm
FeederBase.stl
FeederCover.stl
PressureArm.stl
QRCap-16mm-optional.stl
TapeLever.stl

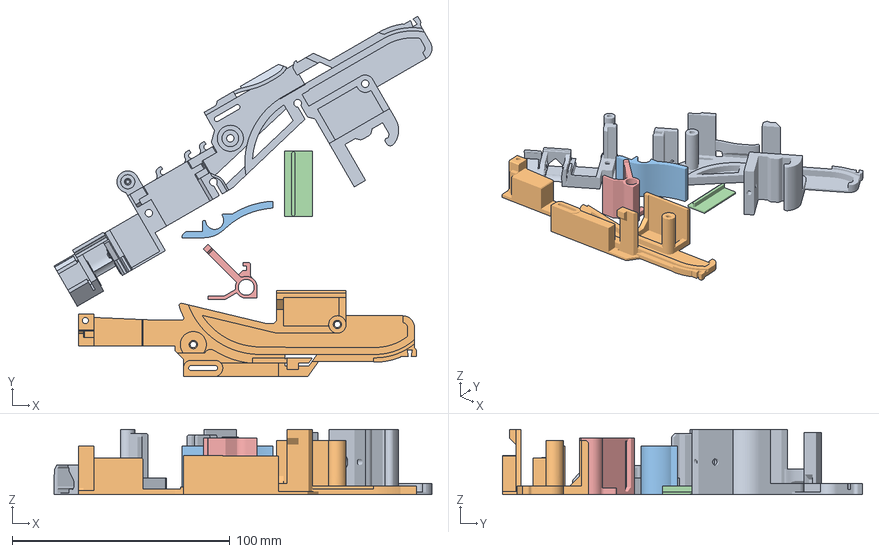
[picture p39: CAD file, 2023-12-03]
3D/24mm/_max-feeder-24mm-plate.3mf
173.5 x 165.4 x 29.9 mm
FeederBase.stl
FeederCover.stl
PressureArm.stl
QRCap-24mm-optional.stl
TapeLever.stl

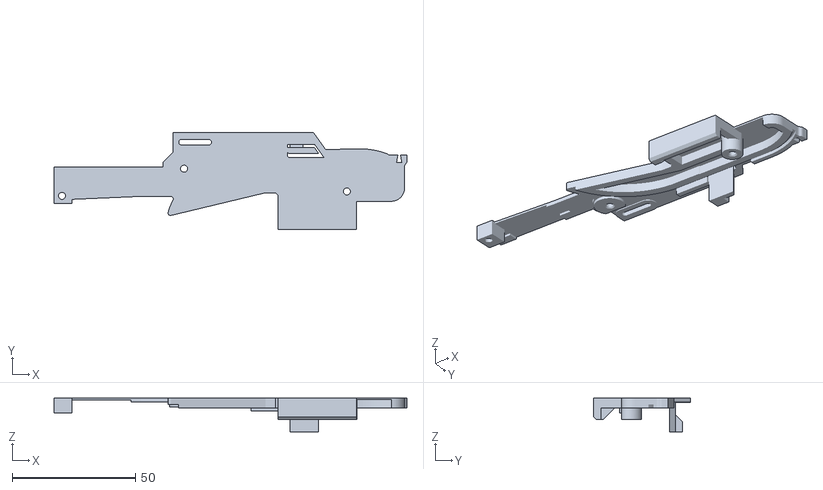
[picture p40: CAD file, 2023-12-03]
3D/8mm/FeederCover.stl
143.3 x 39.5 x 13.7

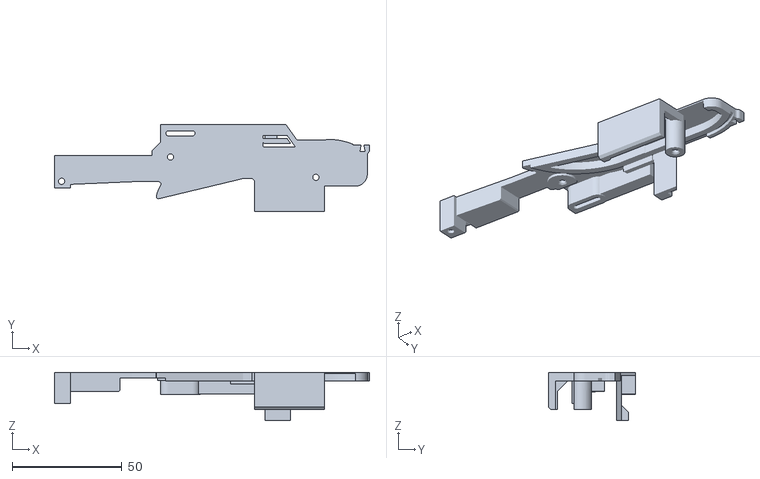
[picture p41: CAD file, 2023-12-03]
3D/16mm/FeederCover.stl
143.3 x 39.5 x 21.9

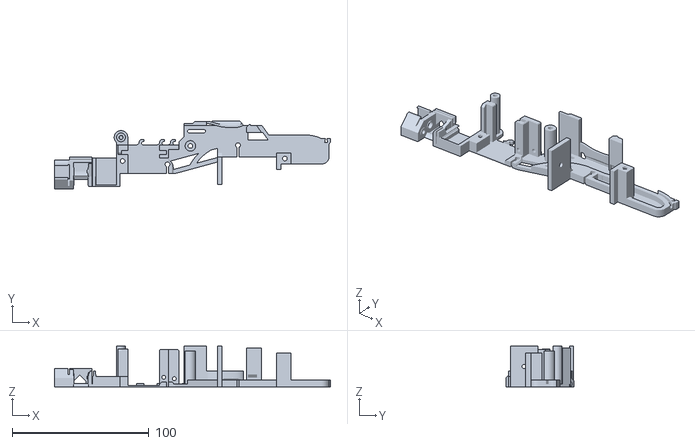
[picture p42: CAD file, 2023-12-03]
3D/24mm/2040-FeederBase.stl
201.9 x 50.0 x 29.9

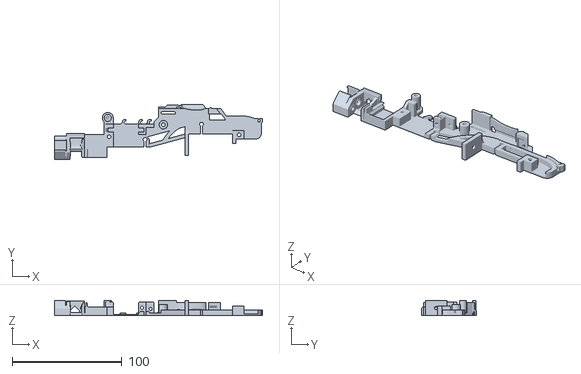
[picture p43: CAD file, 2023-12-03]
3D/8mm/2040-FeederBase.stl
189.9 x 50.0 x 13.7

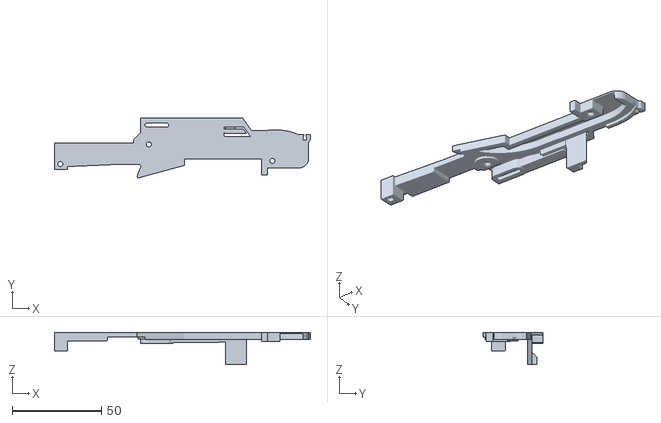
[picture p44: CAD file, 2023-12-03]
3D/12mm/2040-FeederCover.stl
143.3 x 33.6 x 17.9

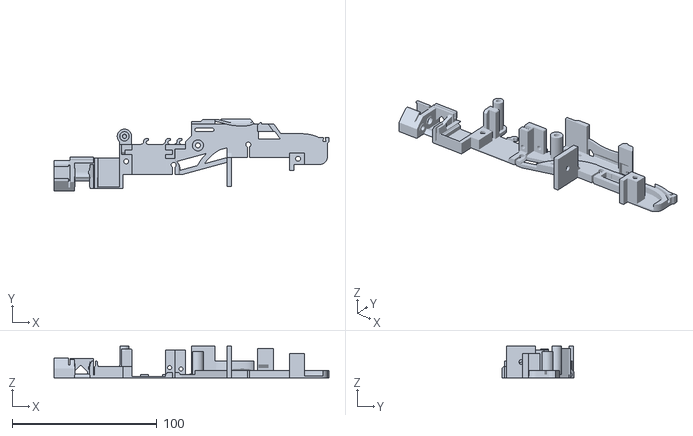
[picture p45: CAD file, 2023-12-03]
3D/16mm/2040-FeederBase.stl
189.9 x 50.0 x 21.9

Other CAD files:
3D/12mm/DIN-FeederBase.stl
3D/24mm/FeederCover.stl
3D/8mm/DIN-FeederCover.stl
3D/12mm/DIN-FeederCover.stl
3D/12mm/1mm-20deg-7t-m3-0.4mm-nozzle-0.05mm.stl
3D/12mm/1mm-20deg-7t-m3-0.4mm-nozzle-0.10mm.stl
3D/12mm/1mm-20deg-7t-m3-0.4mm-nozzle-0.15mm.stl
3D/12mm/1mm-20deg-7t-m3-0.4mm-nozzle-0.20mm.stl
3D/12mm/1mm-20deg-7t-m3-0.4mm-nozzle.stl
3D/12mm/1mm-20deg-8t-key-axel-0.4mm-nozzle-0.05mm.stl
3D/12mm/1mm-20deg-8t-key-axel-0.4mm-nozzle-0.10mm.stl
3D/12mm/1mm-20deg-8t-key-axel-0.4mm-nozzle-0.15mm.stl
3D/12mm/1mm-20deg-8t-key-axel-0.4mm-nozzle-0.20mm.stl
3D/12mm/1mm-20deg-8t-key-axel-0.4mm-nozzle.stl
3D/12mm/FeederBase.stl
3D/12mm/Poker-0.4mm-nozzle-0.8mm-pcb.stl
3D/12mm/Poker-0.4mm-nozzle-no-pcb-legacy.stl
3D/12mm/PokerArm.stl
3D/12mm/PressureArm.stl
3D/12mm/PressureArmWasher-0.4mm-nozzle.stl
3D/12mm/QRCap-12mm-optional.stl
3D/12mm/TapeLever.stl
3D/12mm/WedgeClip-100-infill-optional.stl
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

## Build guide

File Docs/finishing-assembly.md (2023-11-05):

# Finishing Assembling the Max Feeder

You will need the following components to finish assembling the Max Feeder

- Servo poker arm
- Max Feeder PCB
- Motor installed in Feeder Base
- 5x M3 6mm screws
- 2x M3 20mm screws
- Replacement Pen Spring
- Latex free Orthodontic Elastic band
- FeederCover 3D print
- PressureArm 3D print
- PressureArmWasher-0.4mm-nozzle 3D print
- TapeLever 3D print
- Wedge 3D print - optional
- T-nut - optional

Don't want to source all these parts?
[Buy the kit!](https://store.curlytalegames.com/pages/max-feeders)

Note: the leaf spring has been combined with the Feeder Base 3D file. The instructions are still correct, but the photos in the documentation need to be updated. 

## Instructions

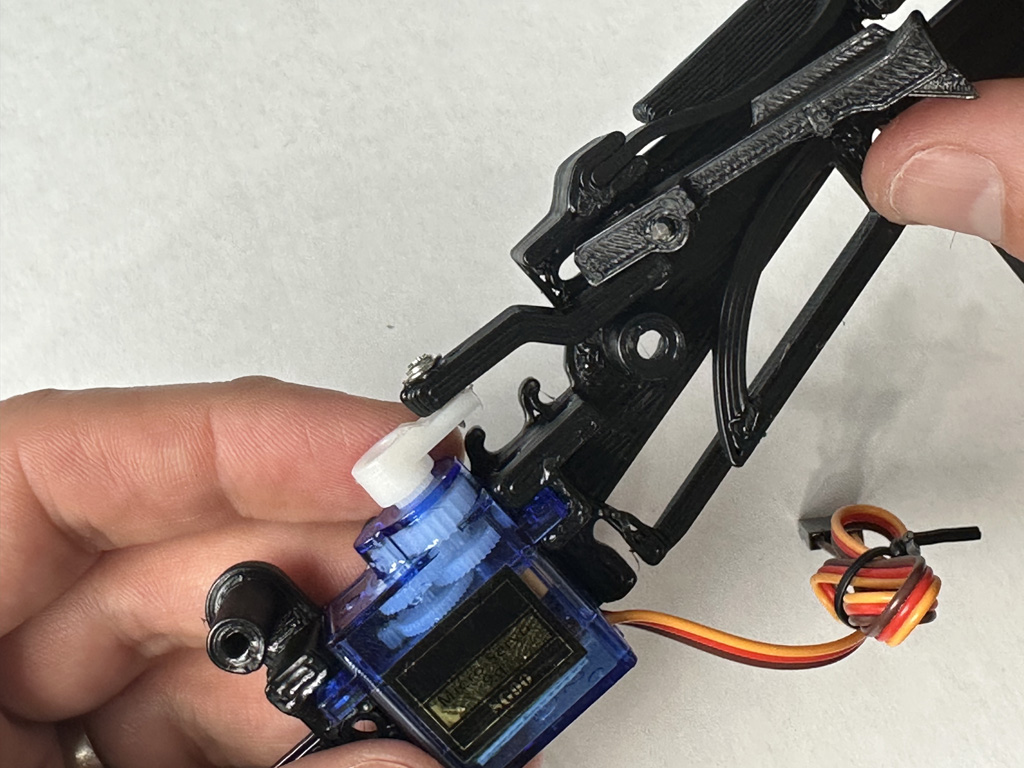
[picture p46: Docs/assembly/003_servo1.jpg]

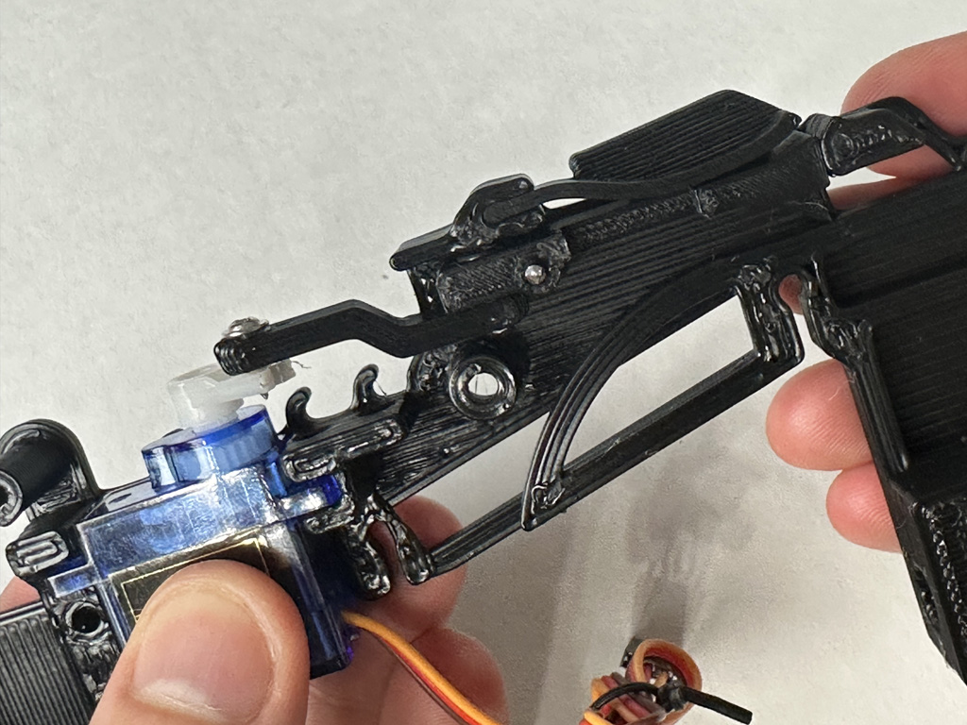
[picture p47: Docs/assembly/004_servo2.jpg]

Push the servo arm assembly into the slot on the Feeder Base

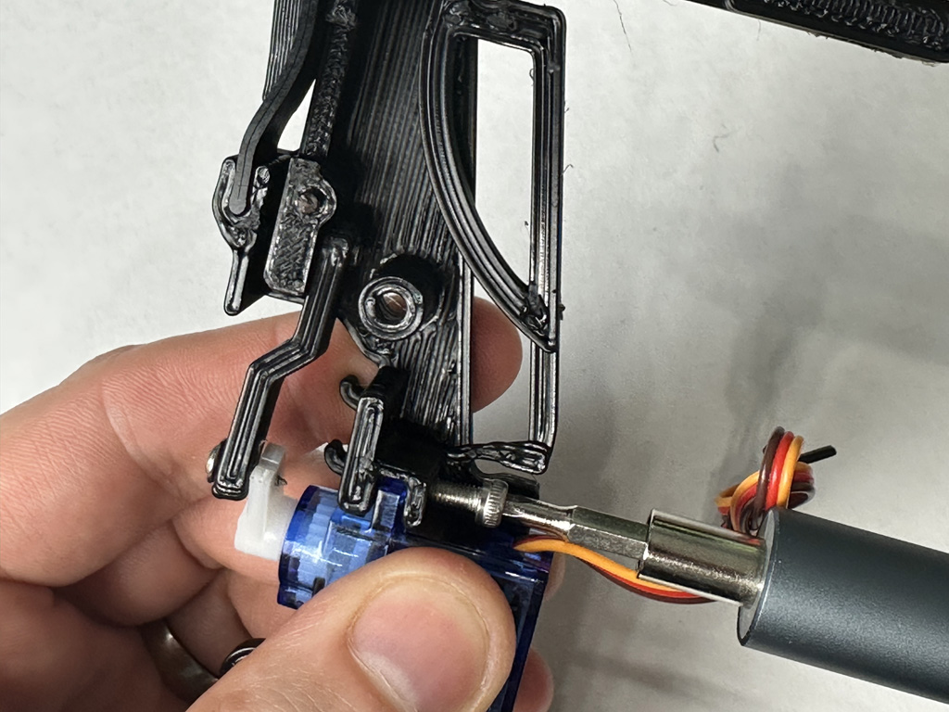
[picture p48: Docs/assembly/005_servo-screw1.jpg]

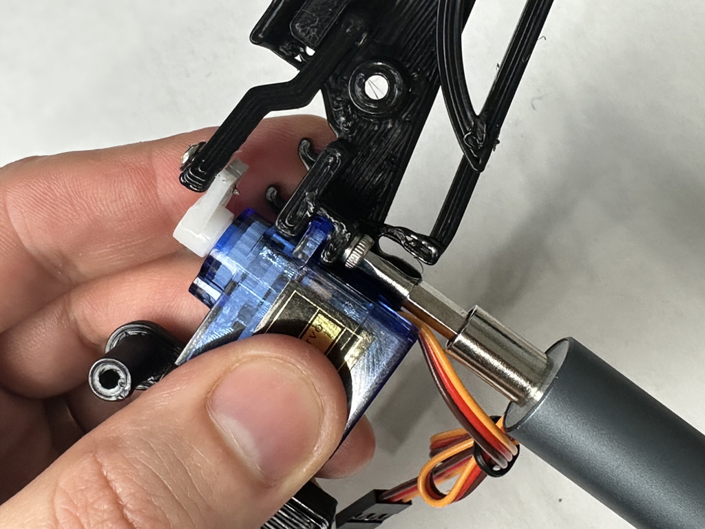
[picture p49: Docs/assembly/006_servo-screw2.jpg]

Screw the servo into the Feeder Base

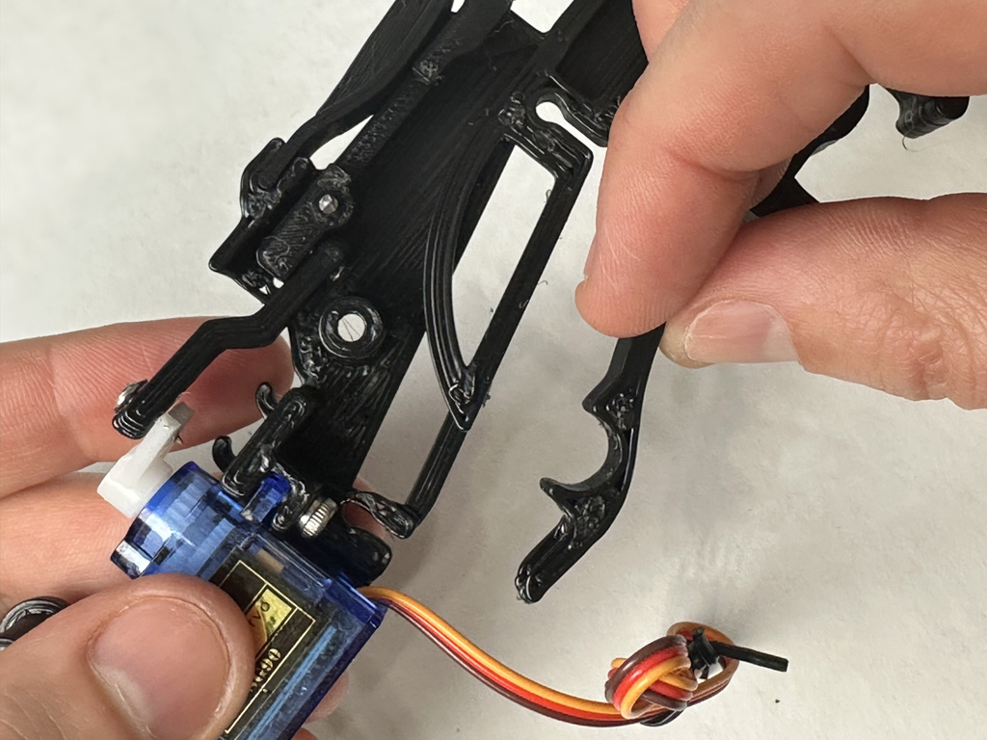
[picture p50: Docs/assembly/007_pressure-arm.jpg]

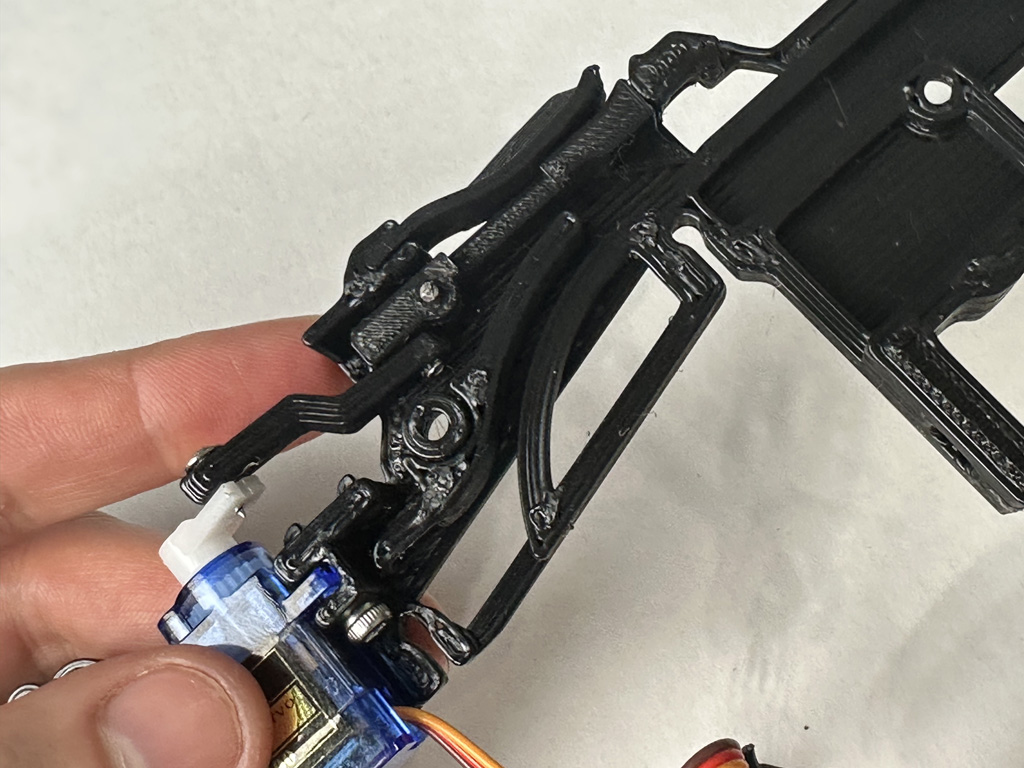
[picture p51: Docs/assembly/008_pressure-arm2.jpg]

Position the pressure arm onto the feeder base like shown

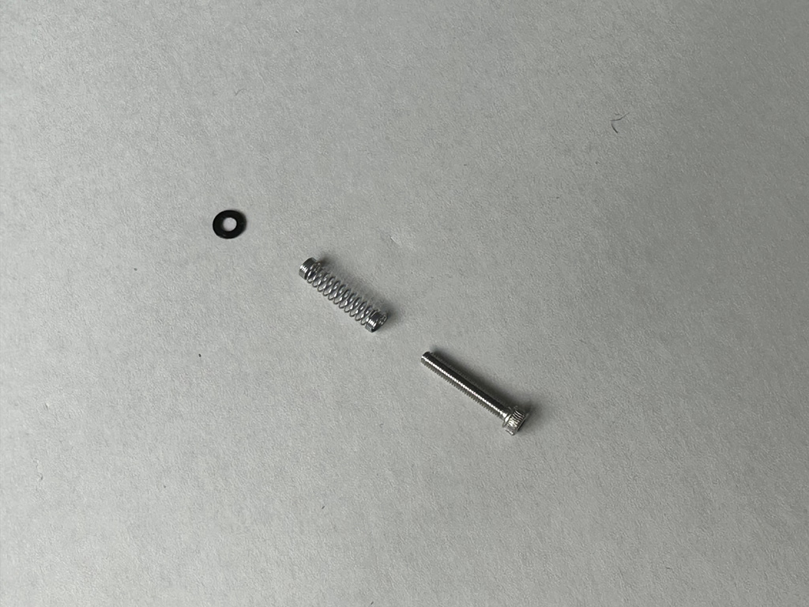
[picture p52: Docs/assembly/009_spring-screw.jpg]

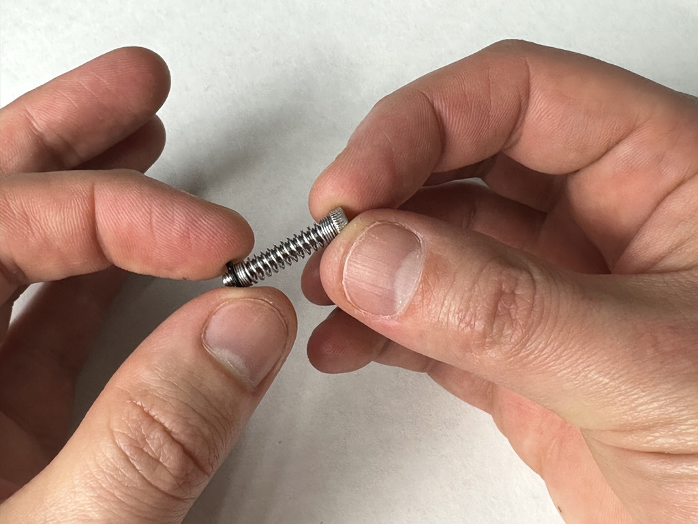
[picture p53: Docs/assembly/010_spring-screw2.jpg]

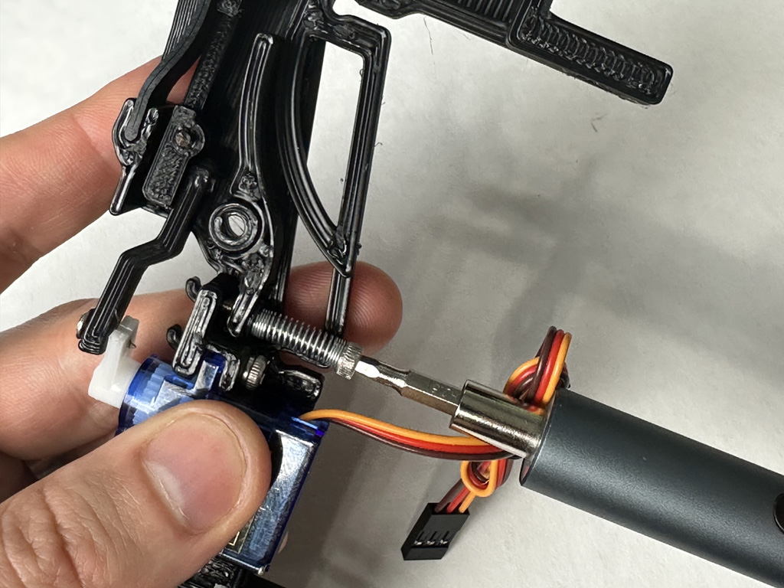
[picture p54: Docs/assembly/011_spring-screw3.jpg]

Slide the pen spring onto the M3 20mm screw, and then slide the pressure arm washer 3D print on top of that. The washer will allow the spring to slide without getting stuck.

Screw the M3 20mm screw into the Feeder Base as shown. Only screw it in a few millimeters, the sping should be able to still move.

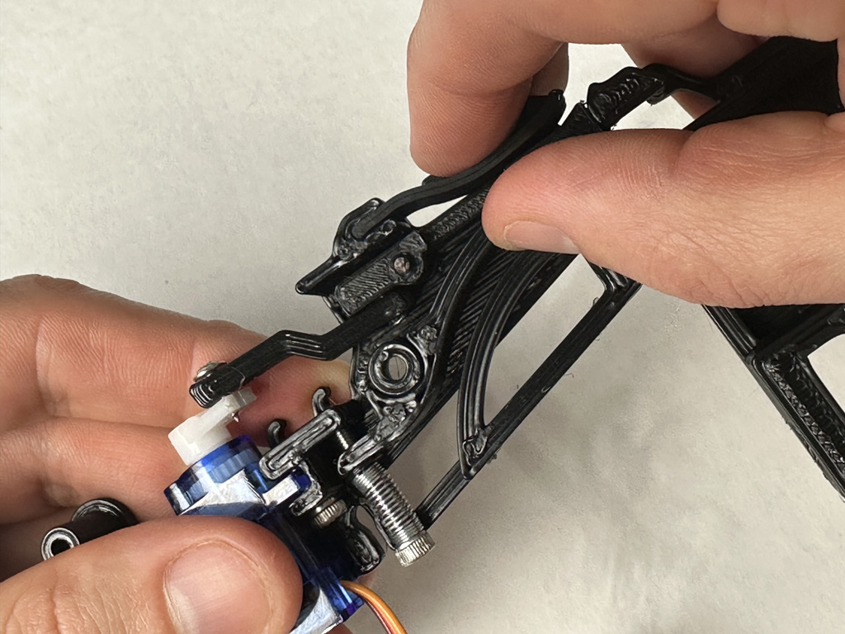
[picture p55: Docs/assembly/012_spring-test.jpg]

Test to make sure the spring can compress and the pressure arm can move.

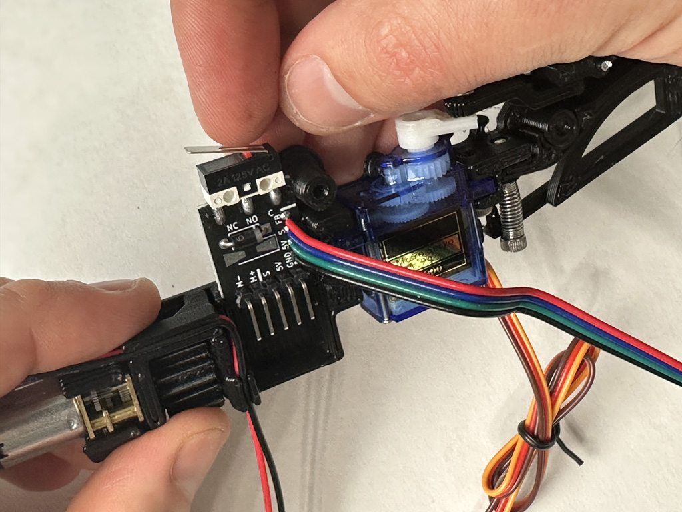
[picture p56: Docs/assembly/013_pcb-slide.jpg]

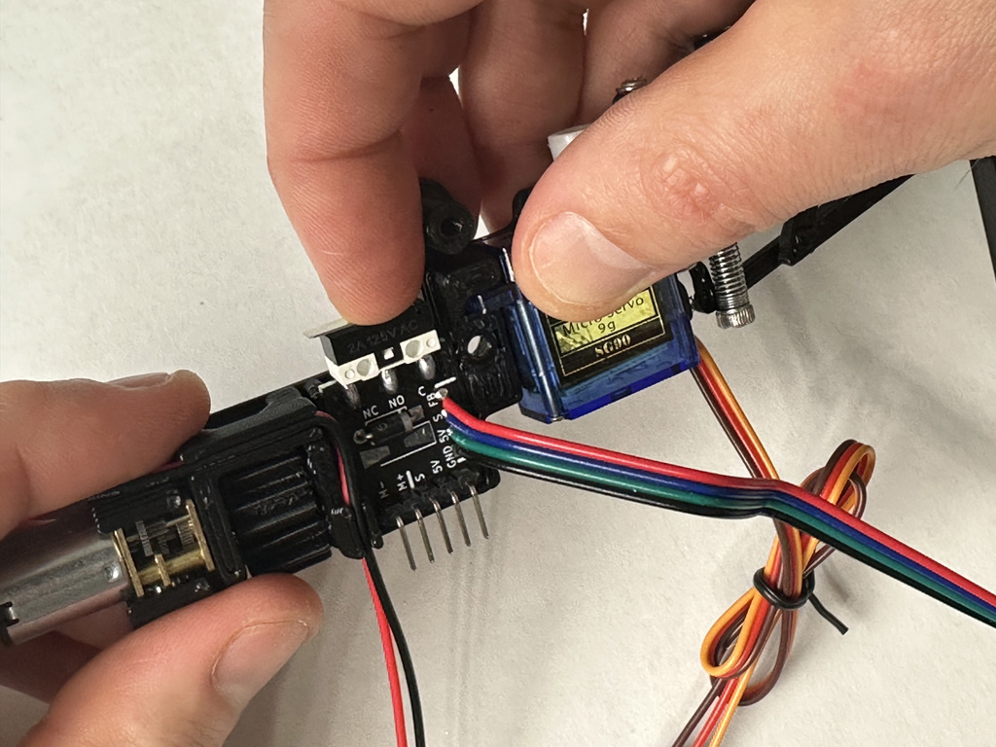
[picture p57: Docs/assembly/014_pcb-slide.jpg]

There is a slot for the Max Feeder PCB to slide into. Push it into place, but be careful not to press on the wires, they can be easily pulled out at this point.

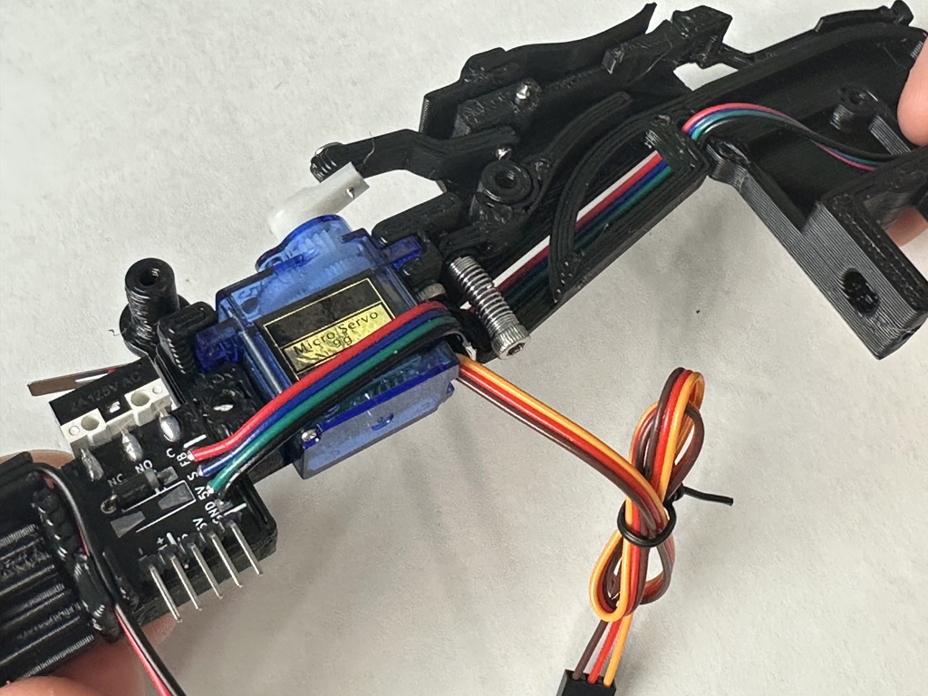
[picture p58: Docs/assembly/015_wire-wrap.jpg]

Wrap the wires from the PCB around the strain reliefs.

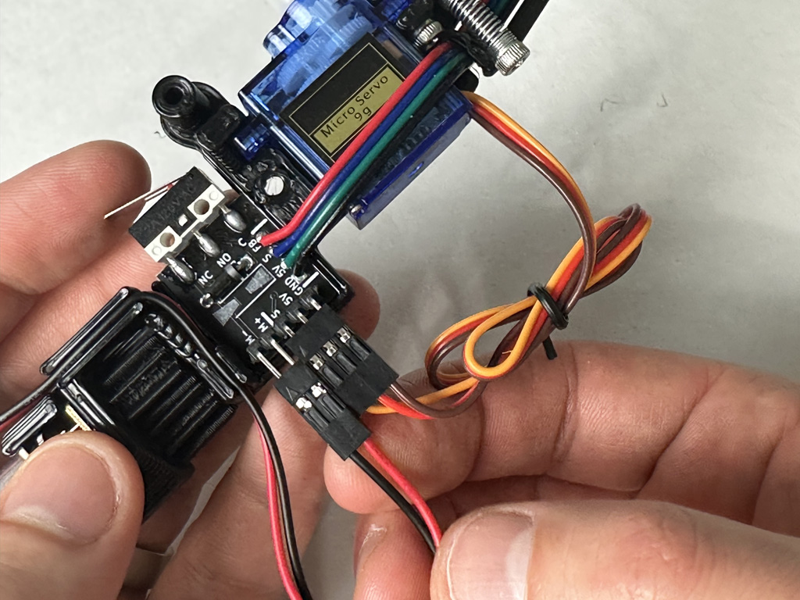
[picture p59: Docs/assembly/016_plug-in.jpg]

Plug the servo and motor into the angled header on the bottom of the PCB. The brown wire on the servo goes to GND and the orange wire goes to S (for signal). The black wire on the motor should go to M- and the red wire should go to M+. 

If the cover tape ever gets jammed you can flip the motor plug to reverse the direction of the motor.

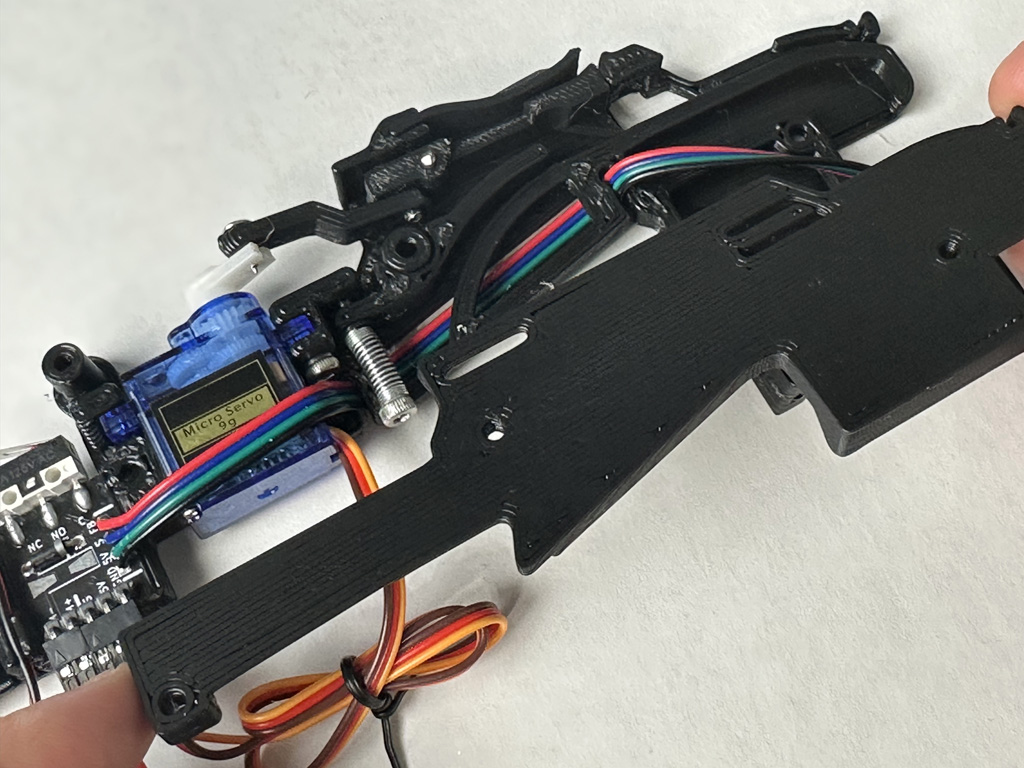
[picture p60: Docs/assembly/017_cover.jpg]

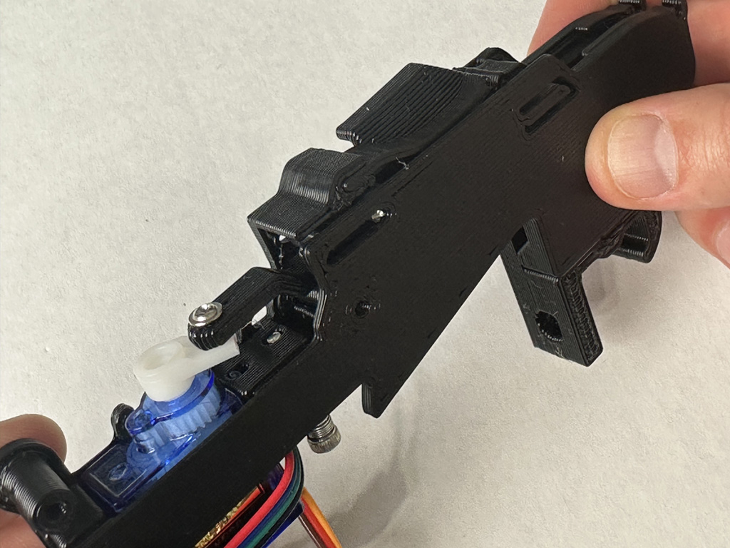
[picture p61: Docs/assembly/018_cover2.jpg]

Press the Feeder Cover onto the Feeder Base. It can be tricky to line up.

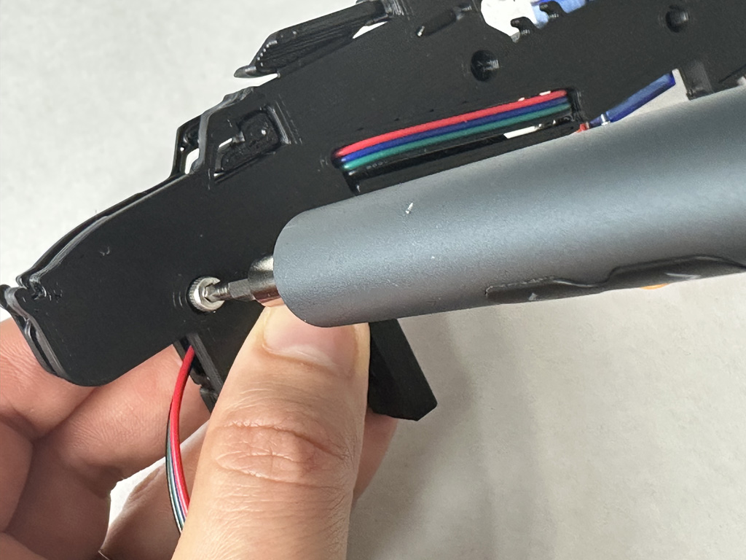
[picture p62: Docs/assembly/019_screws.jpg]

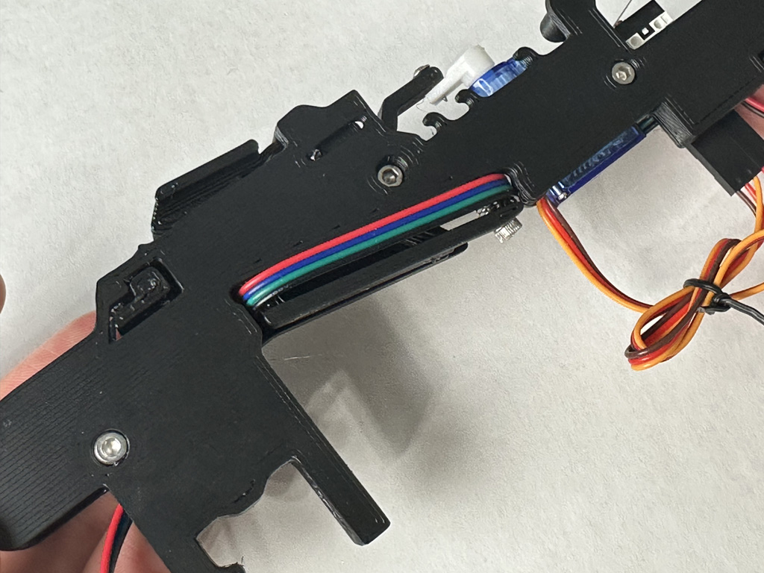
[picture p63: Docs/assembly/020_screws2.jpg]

Flip the feeder over and screw the 3x M3 6mm screws into the holes. Firmly hold the cover on and screw the M3 screws in all the way, but be careful not to overtighten them, you are screwing into plastic.

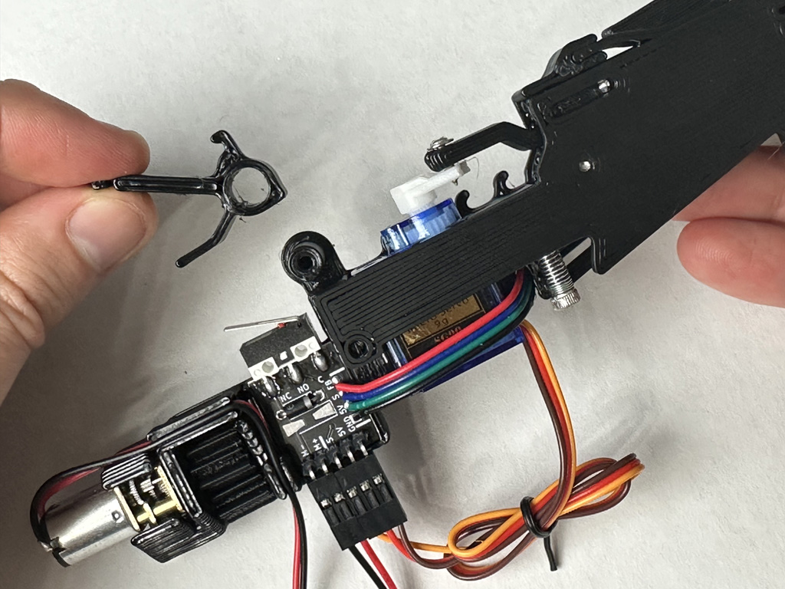
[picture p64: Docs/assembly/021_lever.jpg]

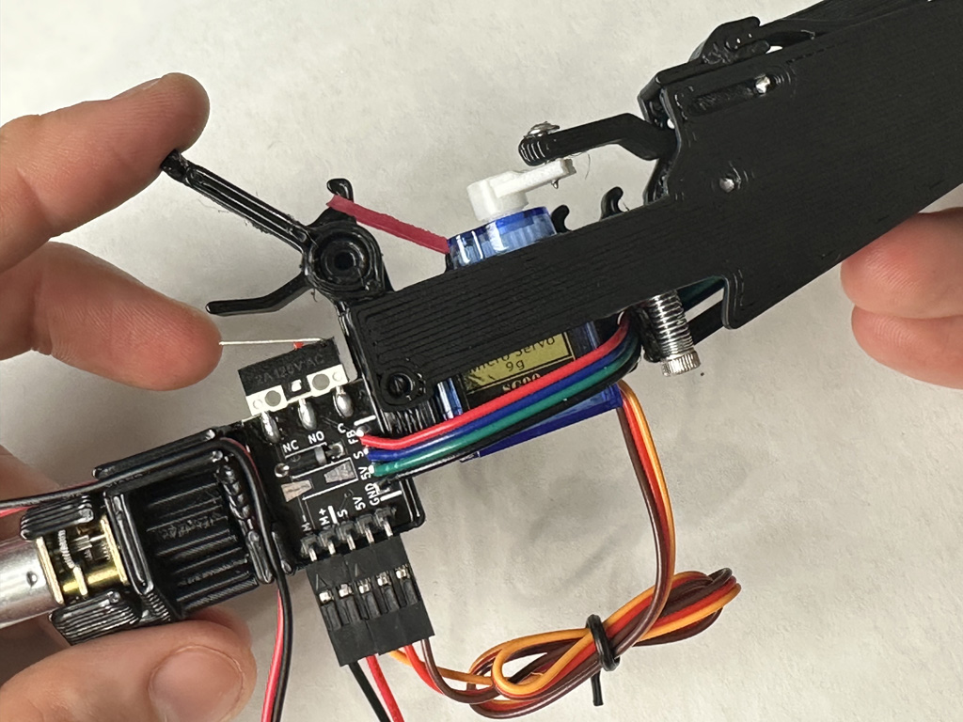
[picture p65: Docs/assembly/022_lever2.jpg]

Slide the Tape Lever on the axel above the PCB, and using an elastic attach the lever to the closest hook on the Feeder Base as shown.

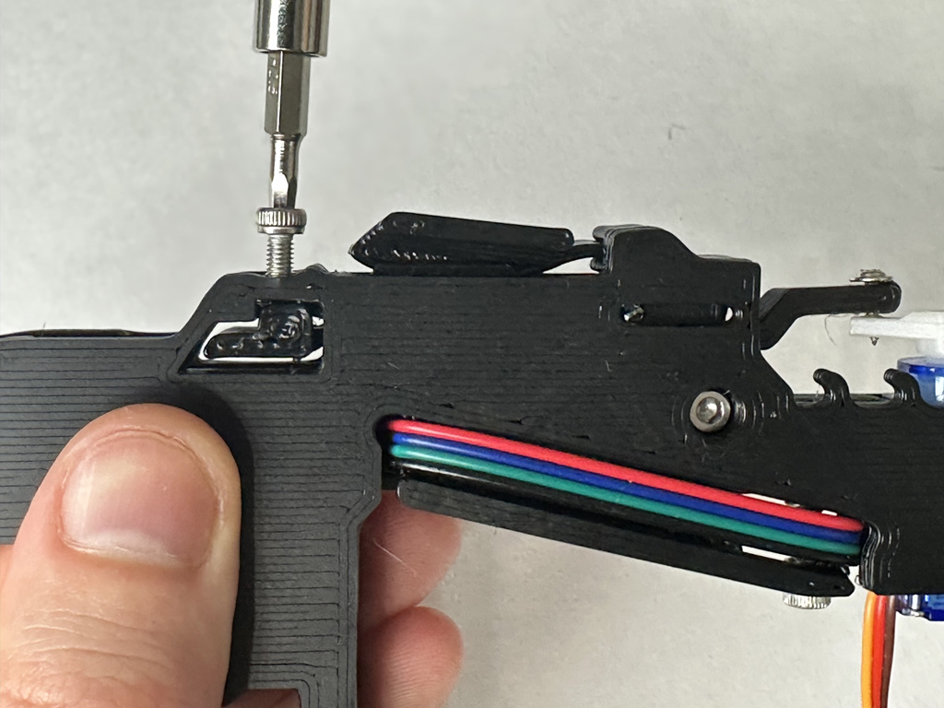
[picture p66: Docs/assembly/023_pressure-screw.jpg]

Some tapes will require a little more friction for the servo to ratchet properly. Screw a M3 6mm screw into the front of the feeder to press down slightly on the tape.

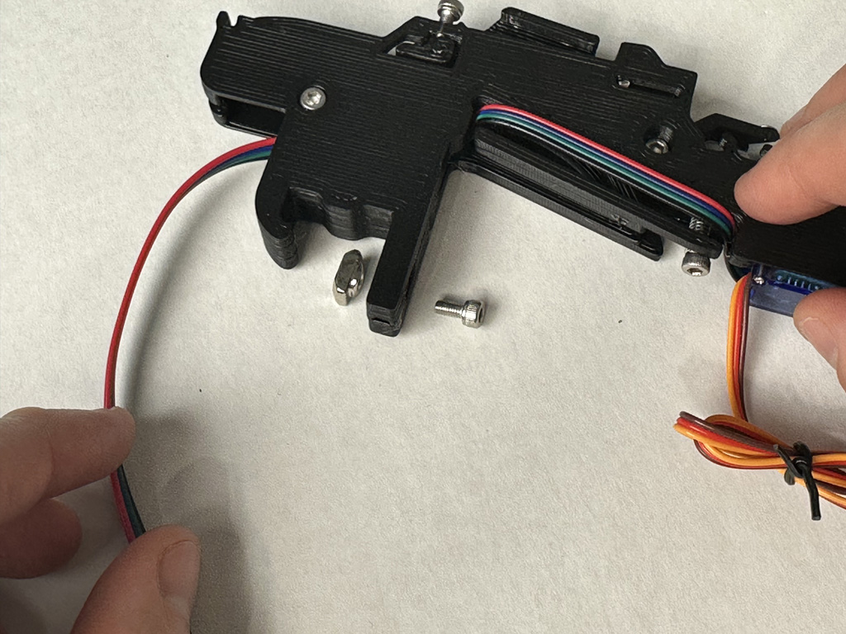
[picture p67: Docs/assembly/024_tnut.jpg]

Optional - Clip the feeder onto some 2020 aluminum extrusion and using an M3 T-nut and an M3 6mm screw tighten the feeder down to the frame of your Pick and Place machine.

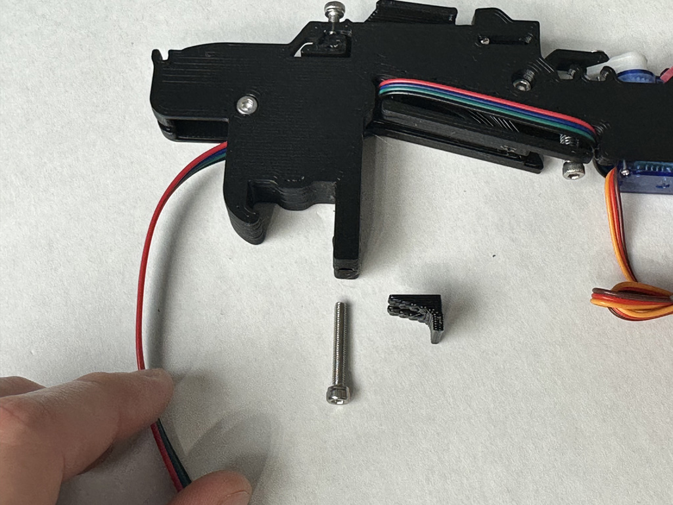
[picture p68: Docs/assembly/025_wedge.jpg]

Optional - If you don't want to bolt the feeder down, you can screw an M3 20mm screw into the bottom of the feeder and use the 3D printed wedge to hold the feeder in place. This allows you to more easily remove or reposition the feeder.

<video src="https://user-images.githubusercontent.com/25337335/216263875-0b8626d9-b433-4cdb-8888-c90433fe03b6.mp4" data-canonical-src="https://user-images.githubusercontent.com/25337335/216263875-0b8626d9-b433-4cdb-8888-c90433fe03b6.mp4" controls="controls" muted="muted" class="d-block rounded-bottom-2 border-top width-fit" style="max-height:640px; min-height: 200px">
</video>

We want the servos to all have the same start and end position. To ensure that, unplug the servo horn from the servo, plug the JST cable into the Max Feeder Shield, and double click the tape lever to actuate the servo.

Now re-attach the servo horn facing straight towards the front of the feeder.

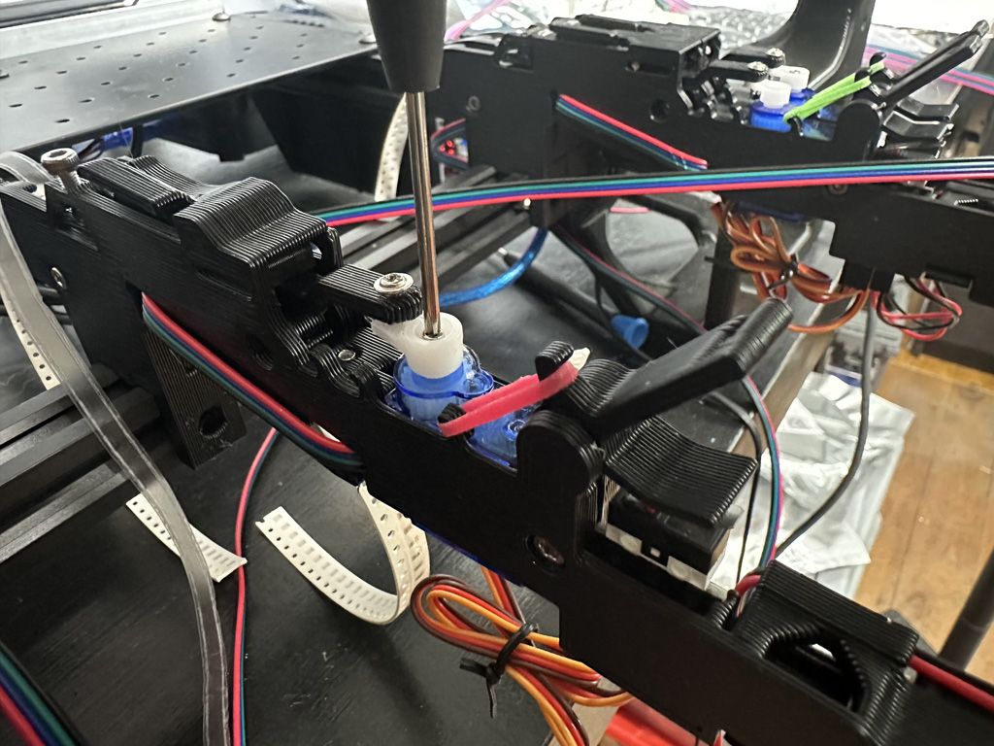
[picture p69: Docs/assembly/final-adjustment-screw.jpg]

Using the tiny screw included in the servo horn kit, screw the servo horn onto the servo.

### [Next Step: GcodeDriver and AutoFeeder Setup in Open PnP](openpnp.md)

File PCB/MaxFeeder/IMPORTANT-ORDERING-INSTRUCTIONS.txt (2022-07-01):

When ordering add this to the comments for the PCB:

Please V-CUT as indicated in the Eco1_User gerber file.

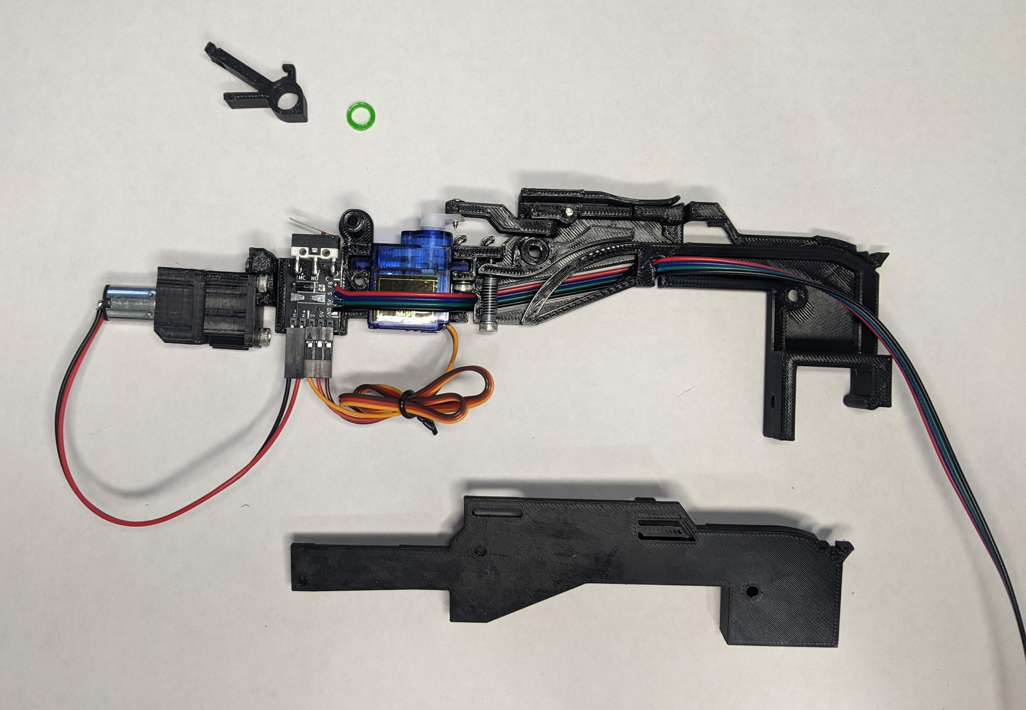
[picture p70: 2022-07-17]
Docs/assembly_06_lever.jpg

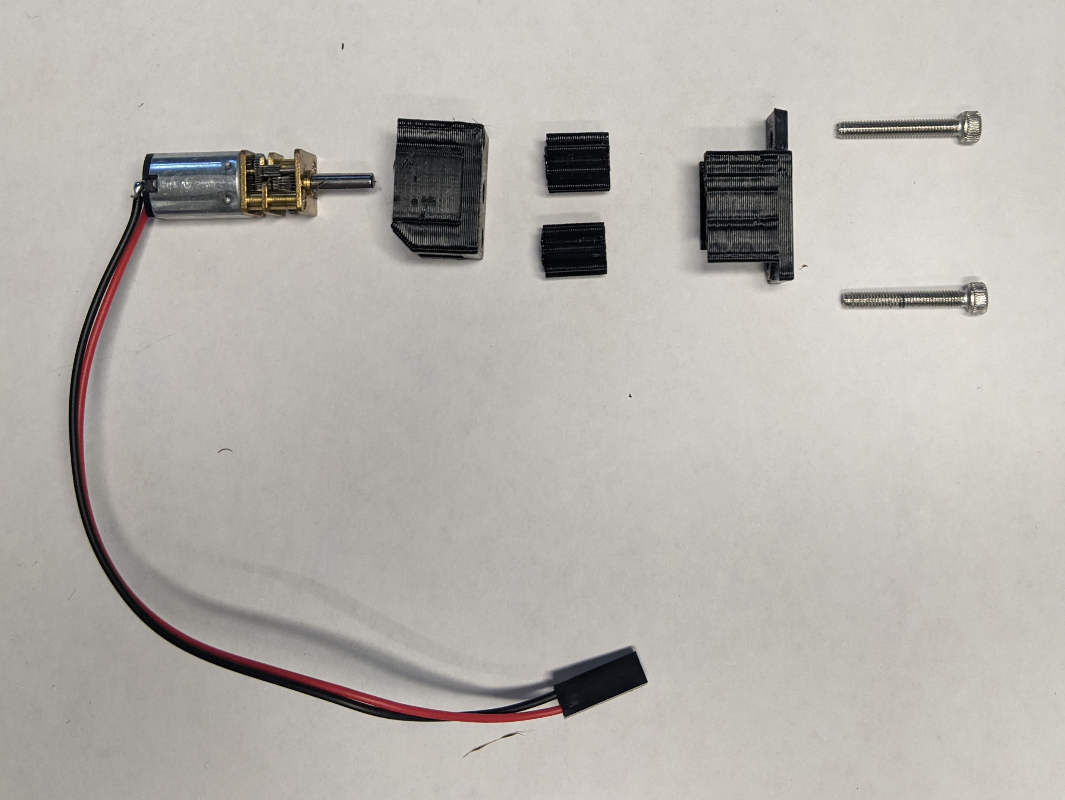
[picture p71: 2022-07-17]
Docs/assembly_04_tape_motor.jpg

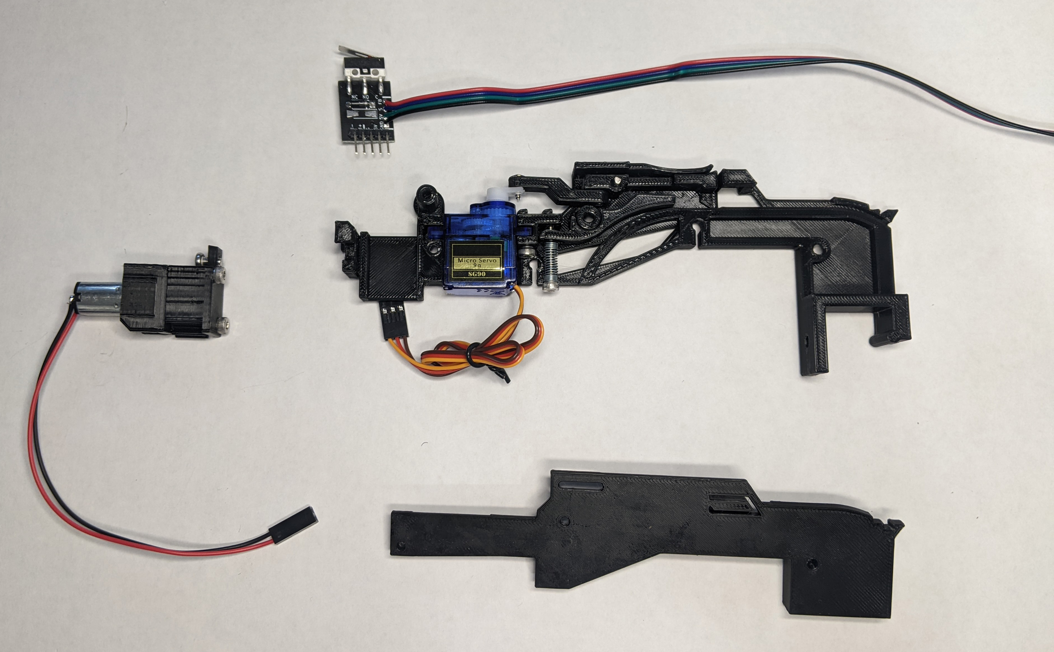
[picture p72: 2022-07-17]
Docs/assembly_05_pcb_motor.jpg

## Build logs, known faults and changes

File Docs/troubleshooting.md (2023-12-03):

# Max Feeder Troubleshooting Guide

## The n20 Won't Stop Spinning / My Max Feeders Aren't Actuating

The n20 motor will spin if you don't have tape loaded into the feeder.

The microswitch is what controls the motor, when it's pressed down it cuts power to the motor, and sends a signal to the Arduino Mega letting it know that the slack tape has been pulled through the gears.

The firmware on the Arduino Mega sends an `ok` message over serial when the microswitch is pressed. This lets Open PnP know the feeding was successful. Open PnP won't let you feed more parts until it gets an `ok`.

To fix these problems you can either unplug feeders you aren't using, or what I like to do is wedge some 0.1" male header under the tape lever like this:

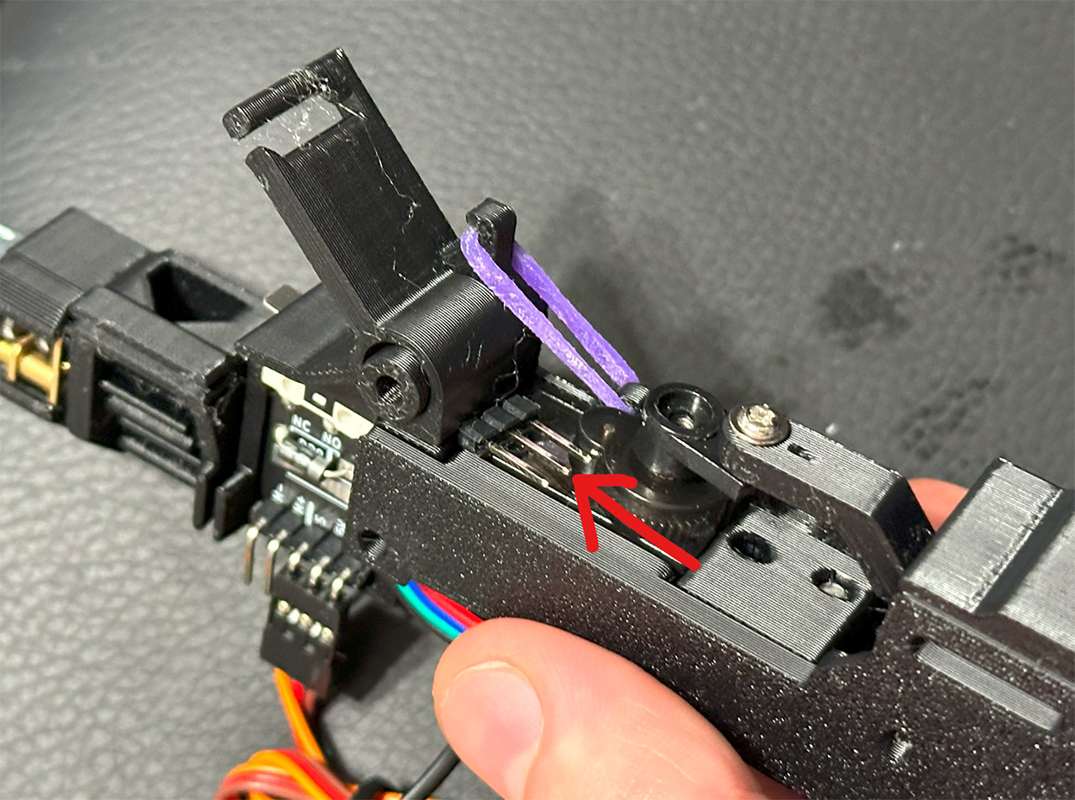
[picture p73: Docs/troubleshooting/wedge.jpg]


## Servo Not Ratcheting Tape

There can be a few reasons why the tape isn't being pushed forward. Here a few things to check:

* Make sure The tip of the poker is sharp and pointy. Cut it with a sharp fresh knife blade. This should not be an issue with the new PCB poker tips.
* If the tape moves back and forth when the servo actuates, make sure to tighten the screw on the top front of the Max Feeder to put pressure on the tape.
* If the servo actuates but the tape doesn't move, loosen the screw on the top front of the Max Feeder.
* If you are rough with the cable soldered to the PCB sometimes one of the wires might break and get disconnected or have intermitten connections. If you resolder the wires to the PCB it should fix the issue. Usually this isn't an issue unless you take your feeders apart and put them back together a bunch.

## Tape Gears Binding

There are a couple things that could bind the gears, here are a few things that have happened and how to fix it.

### Loose Part Jammed in Gears
After doing a lot of test feeds I had a 0805 resistor get stuck to the adhesive on the cover tape. The resistor somehow made it all the way back to the tape gears and jammed them. Unscrew the idler gear and pull out the n20 motor to remove the loose part. Under normal opperation this wouldn't happen. The pick and place machine would pick up the part so you wouldn't have loose parts.

### Excessive Pressure on Idler Gear

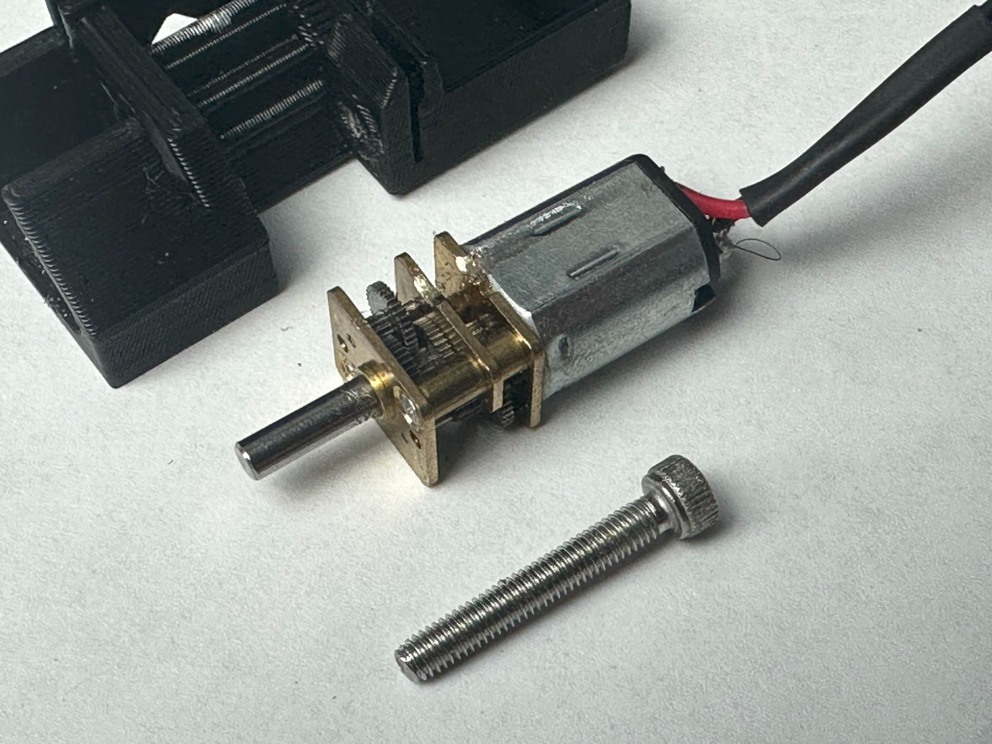
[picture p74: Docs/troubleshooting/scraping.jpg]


One user reported that the M3 20mm screw was putting exessive pressure on the idler gear causing the motor to bind. In order for the gears to hold the tape, the M3 20mm screw needs to be very close to the n20 motor. It's normal for the head of the M3 20mm screw to scrape on the side of the motor, but the gears should be able to turn.

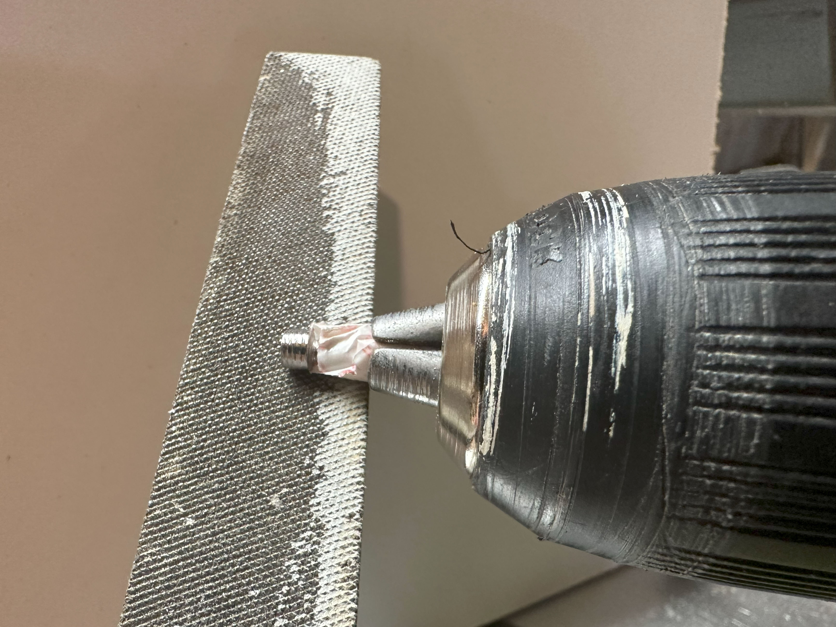
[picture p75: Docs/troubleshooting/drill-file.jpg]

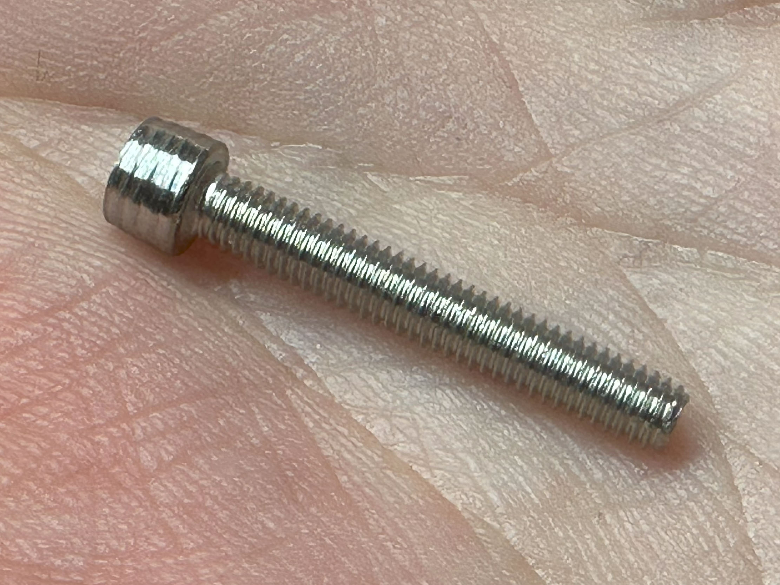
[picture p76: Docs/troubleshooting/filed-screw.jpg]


What fixed it was filing down the head of the screw. Wrap the threads of the screw with some tape, and put it in a drill chuck and press it against the file. 

Alternatively an M3 20mm grub screw could also be used.

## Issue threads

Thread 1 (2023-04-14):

Wrong feeder pcb ? N20-GND is connected  to NO or NC?

indexdb, 2023-04-14:
When the power is turned on, the N20 motor turns continuously. I checked the schematic of the feeder and N20-GND is connected to the NC of the limit switch (Normally closed). So, by default N20-GND is connected  to GND and N20-5v connect to +5V , so as soon as the power is turned on, the N20d motor starts to work.
I think N20-GND should connect to NO terminal of the limit switch.

CurlyTaleGames, 2023-04-25:
Hi indexdb,

That microswitch is doing a lot of things, and the circuit definitely looks odd, but it's normal for the n20 motor to run if there isn't any tape loaded. When the cover tape pulls down on the tape lever it presses the microswitch which disconnects power to the motor.

If you haven't loaded tape into the feeder and don't want the motor to spin all the time, you can either unplug the n20 motor or what I like to do is wedge some male header under the 3d printed lever arm. That will keep the microswitch held down so power isn't being sent to the motor.

Thanks!
-Ben

Closed 2023-04-25.

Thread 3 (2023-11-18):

Clarification regarding length of 2mm pin

joelhauxwell, 2023-11-18:
Hi,

Thanks for sharing this project, im printing parts to build some feeders for my LumenPnP.

There is a guide pin in the BOM - on your main page its described as 2mm x 14mm https://github.com/CurlyTaleGamesLLC/MaxFeeder

On the poker asssebly page its descibed as 13mm long - https://github.com/CurlyTaleGamesLLC/MaxFeeder/blob/main/Docs/poker.md

Can you confirm if 14mm is OK?

Thanks,

Joel.

joelhauxwell, 2023-11-19:
I dug out my vernier and measured - 13mm looks right.

Apologies, i should have done this to start.

Closed 2023-11-19.

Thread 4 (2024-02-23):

Wrong documentation link

casartar, 2024-02-23:
In README.md the link to "Loading and Unloading Tape into Max Feeder" is wrong. It points to https://github.com/CurlyTaleGamesLLC/MaxFeeder/blob/main/Docs/finishing-assembly.md but not https://github.com/CurlyTaleGamesLLC/MaxFeeder/blob/main/Docs/tape.md

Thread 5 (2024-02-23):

PokerTips Issues

casartar, 2024-02-23:
It is unclear from the documentation what the PokerTips are for.
And under [PCB/Power](https://github.com/CurlyTaleGamesLLC/MaxFeeder/tree/main/PCB/PokerTips) there is no information, that the pcb should be 0.8mm thick (at leaset i think it shuold be that way from the documentation). An order-screenshot would be helpful as with the other PCBs.

Just a hint: There are copper points on the top left PokerTips, which are confusing JLCPCB. They ask if they should copy them on all Tips.

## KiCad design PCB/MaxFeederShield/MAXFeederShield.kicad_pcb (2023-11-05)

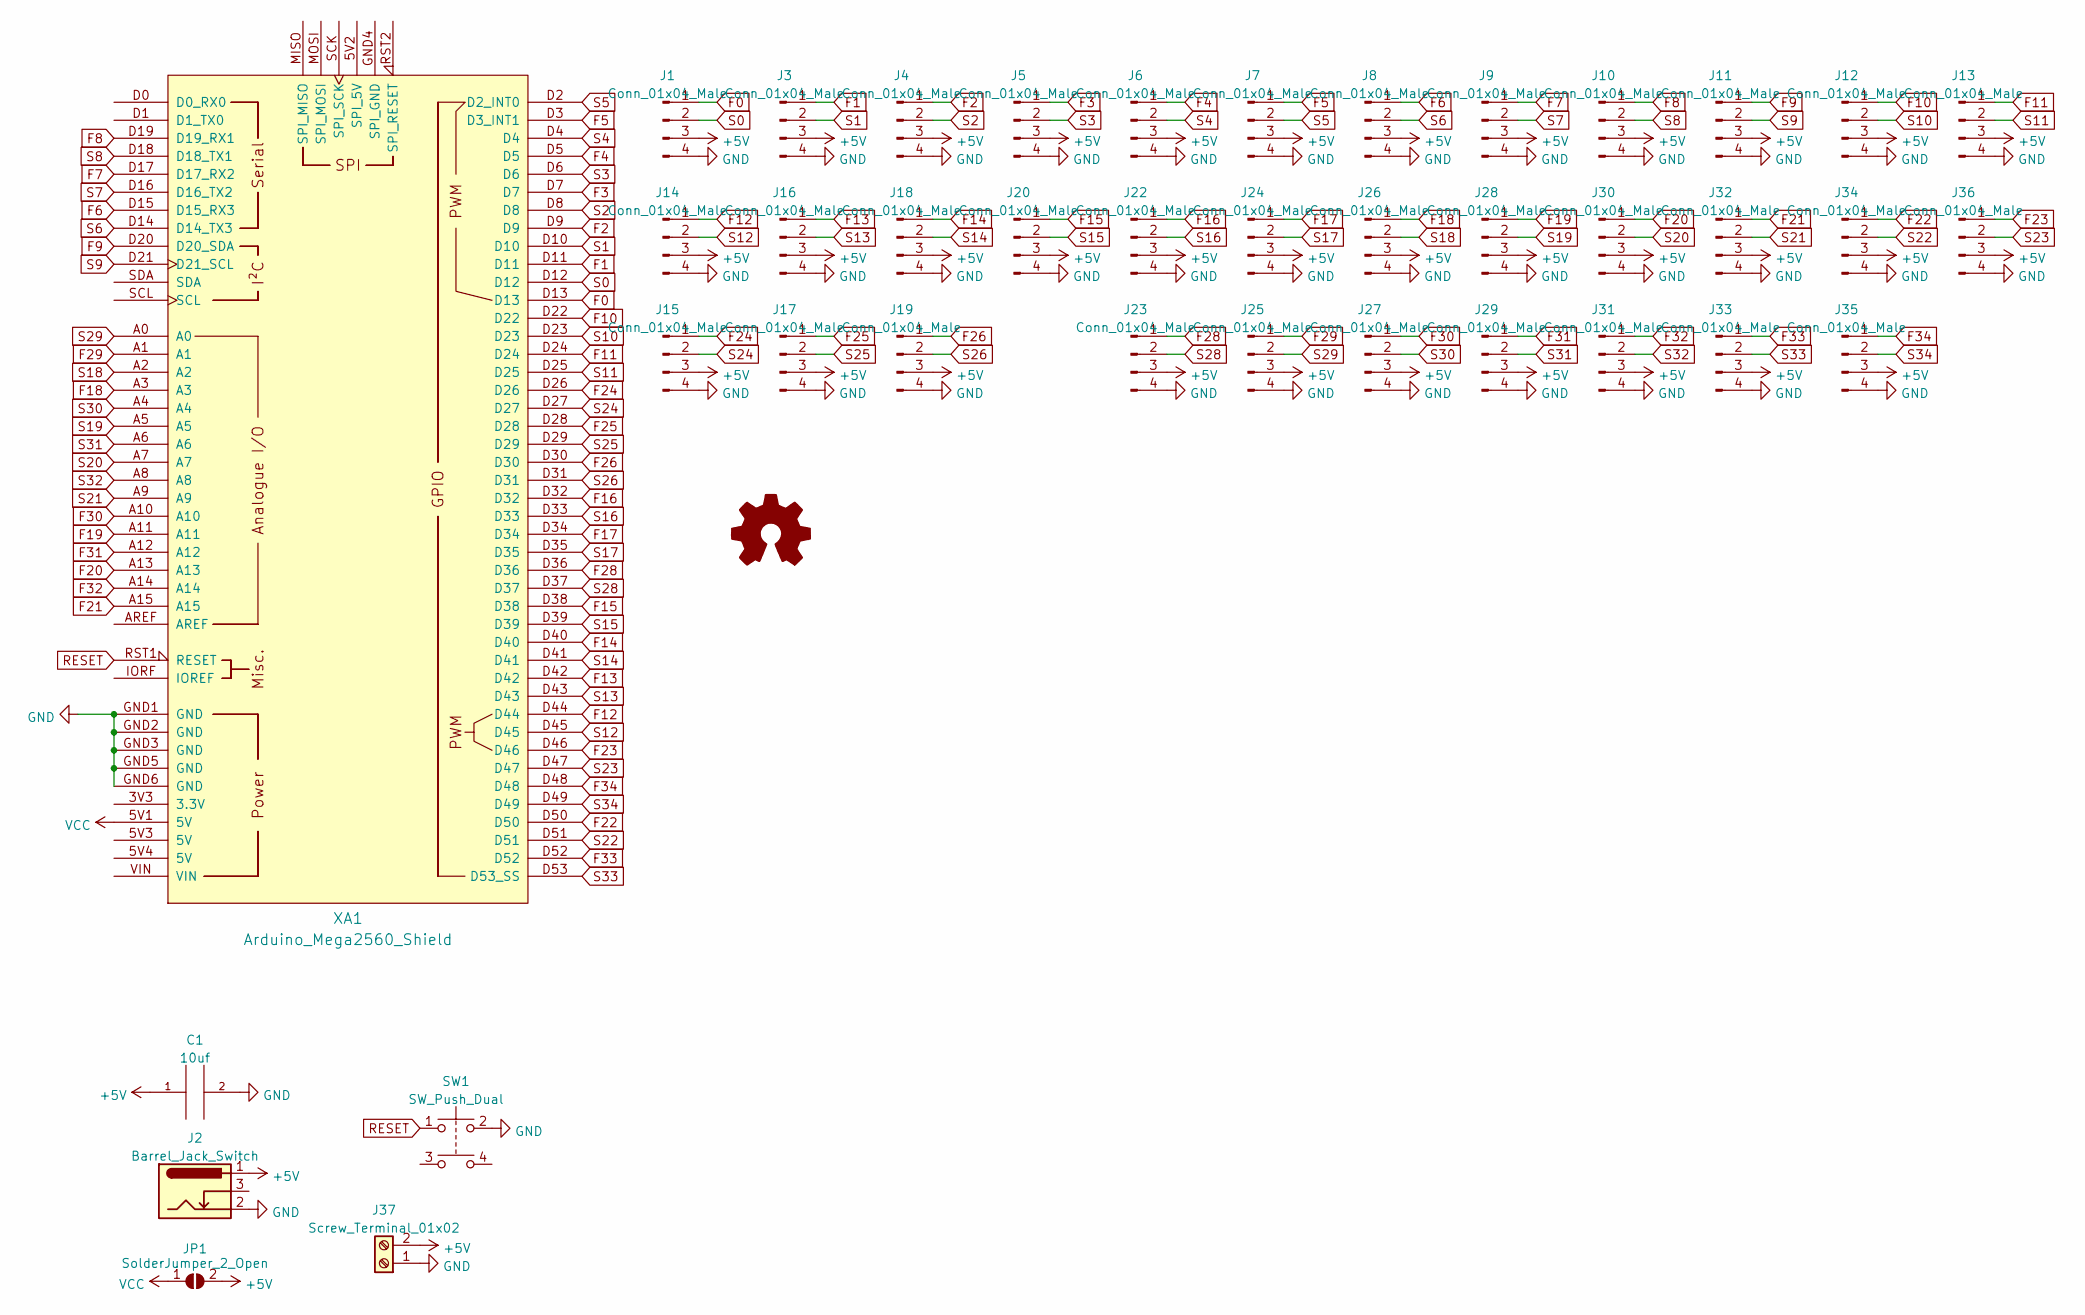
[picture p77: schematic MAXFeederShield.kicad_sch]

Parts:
C1: 10uf; CP_Radial_D5.0mm_P2.50mm
J1, J3, J4, J5, J6, J7, J8, J9, J10, J11, J12, J13, J14, J15, J16, J17, J18, J19, J20, J22, J23, J24, J25, J26, J27, J28, J29, J30, J31, J32, J33, J34, J35, J36: Conn_01x04_Male; JST_EH_B4B-EH-A_1x04_P2.50mm_Vertical_LOCKING
J2: Barrel_Jack_Switch; BarrelJack_Horizontal
J37: Screw_Terminal_01x02; PhoenixContact_MC_1,5_2-G-3.81_1x02_P3.81mm_Horizontal
JP1: SolderJumper_2_Open; SolderJumper-2_P1.3mm_Open_Pad1.0x1.5mm
SW1: SW_Push_Dual; SW_PUSH_6mm
XA1: Arduino_Mega2560_Shield; Arduino_Mega2560_Shield_NO_HOLES

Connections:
+5V: C1.1, J1.3, J2.1, J3.3, J4.3, J5.3, J6.3, J7.3, J8.3, J9.3, J10.3, J11.3, J12.3, J13.3, J14.3, J15.3, J16.3, J17.3, J18.3, J19.3, J20.3, J22.3, J23.3, J24.3, J25.3, J26.3, J27.3, J28.3, J29.3, J30.3, J31.3, J32.3, J33.3, J34.3, J35.3, J36.3, J37.2, JP1.2 (B)
F0: J1.1, XA1.D13
F1: J3.1, XA1.D11
F2: J4.1, XA1.D9
F3: J5.1, XA1.D7
F4: J6.1, XA1.D5
F5: J7.1, XA1.D3 (D3_INT1)
F6: J8.1, XA1.D15 (D15_RX3)
F7: J9.1, XA1.D17 (D17_RX2)
F8: J10.1, XA1.D19 (D19_RX1)
F9: J11.1, XA1.D20 (D20_SDA)
F10: J12.1, XA1.D22
F11: J13.1, XA1.D24
F12: J14.1, XA1.D44
F13: J16.1, XA1.D42
F14: J18.1, XA1.D40
F15: J20.1, XA1.D38
F16: J22.1, XA1.D32
F17: J24.1, XA1.D34
F18: J26.1, XA1.A3
F19: J28.1, XA1.A11
F20: J30.1, XA1.A13
F21: J32.1, XA1.A15
F22: J34.1, XA1.D50
F23: J36.1, XA1.D46
F24: J15.1, XA1.D26
F25: J17.1, XA1.D28
F26: J19.1, XA1.D30
F28: J23.1, XA1.D36
F29: J25.1, XA1.A1
F30: J27.1, XA1.A10
F31: J29.1, XA1.A12
F32: J31.1, XA1.A14
F33: J33.1, XA1.D52
F34: J35.1, XA1.D48
GND: C1.2, J1.4, J2.2, J3.4, J4.4, J5.4, J6.4, J7.4, J8.4, J9.4, J10.4, J11.4, J12.4, J13.4, J14.4, J15.4, J16.4, J17.4, J18.4, J19.4, J20.4, J22.4, J23.4, J24.4, J25.4, J26.4, J27.4, J28.4, J29.4, J30.4, J31.4, J32.4, J33.4, J34.4, J35.4, J36.4, J37.1, SW1.2, XA1.GND1 (GND), XA1.GND2 (GND), XA1.GND3 (GND), XA1.GND5 (GND), XA1.GND6 (GND)
RESET: SW1.1, XA1.RST1 (RESET)
S0: J1.2, XA1.D12
S1: J3.2, XA1.D10
S2: J4.2, XA1.D8
S3: J5.2, XA1.D6
S4: J6.2, XA1.D4
S5: J7.2, XA1.D2 (D2_INT0)
S6: J8.2, XA1.D14 (D14_TX3)
S7: J9.2, XA1.D16 (D16_TX2)
S8: J10.2, XA1.D18 (D18_TX1)
S9: J11.2, XA1.D21 (D21_SCL)
S10: J12.2, XA1.D23
S11: J13.2, XA1.D25
S12: J14.2, XA1.D45
S13: J16.2, XA1.D43
S14: J18.2, XA1.D41
S15: J20.2, XA1.D39
S16: J22.2, XA1.D33
S17: J24.2, XA1.D35
S18: J26.2, XA1.A2
S19: J28.2, XA1.A5
S20: J30.2, XA1.A7
S21: J32.2, XA1.A9
S22: J34.2, XA1.D51
S23: J36.2, XA1.D47
S24: J15.2, XA1.D27
S25: J17.2, XA1.D29
S26: J19.2, XA1.D31
S28: J23.2, XA1.D37
S29: J25.2, XA1.A0
S30: J27.2, XA1.A4
S31: J29.2, XA1.A6
S32: J31.2, XA1.A8
S33: J33.2, XA1.D53 (D53_SS)
S34: J35.2, XA1.D49
VCC: JP1.1 (A), XA1.5V1 (5V)

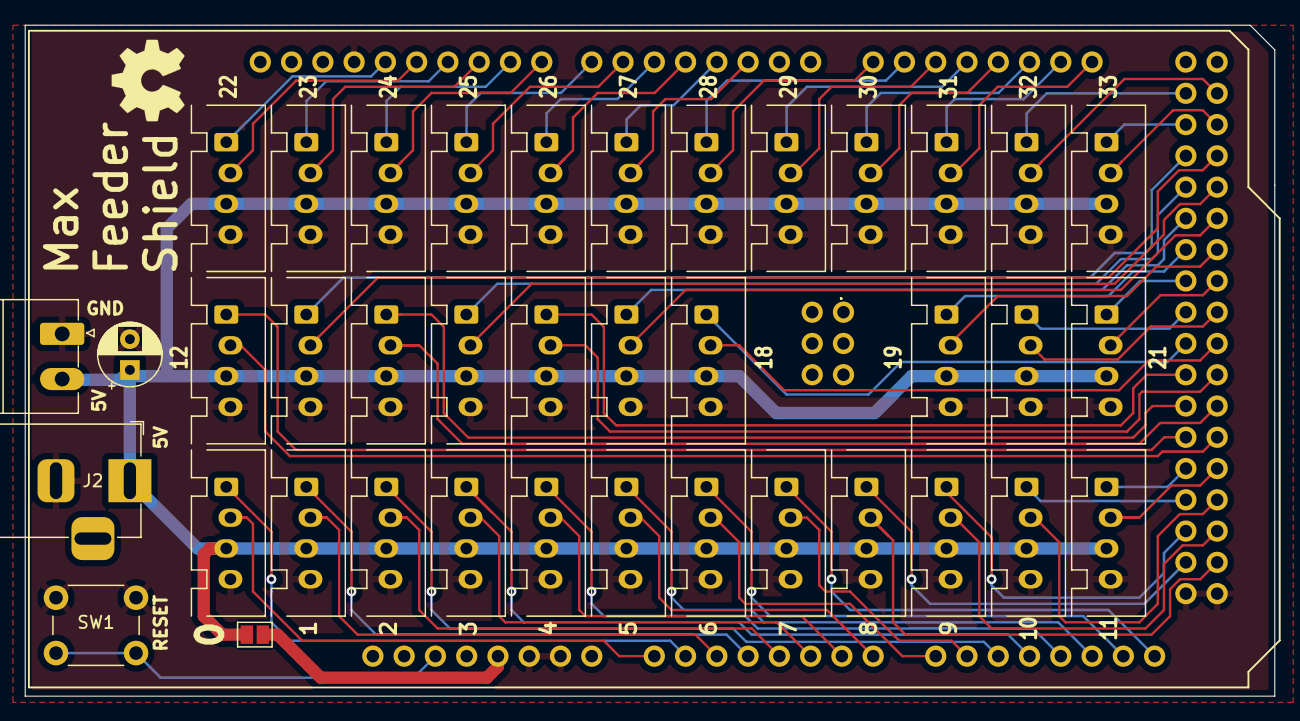
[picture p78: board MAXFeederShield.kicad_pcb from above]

Board: 2 copper layers, 101.5 x 54.5 mm, 40 parts (0 on the bottom side), 72 nets.

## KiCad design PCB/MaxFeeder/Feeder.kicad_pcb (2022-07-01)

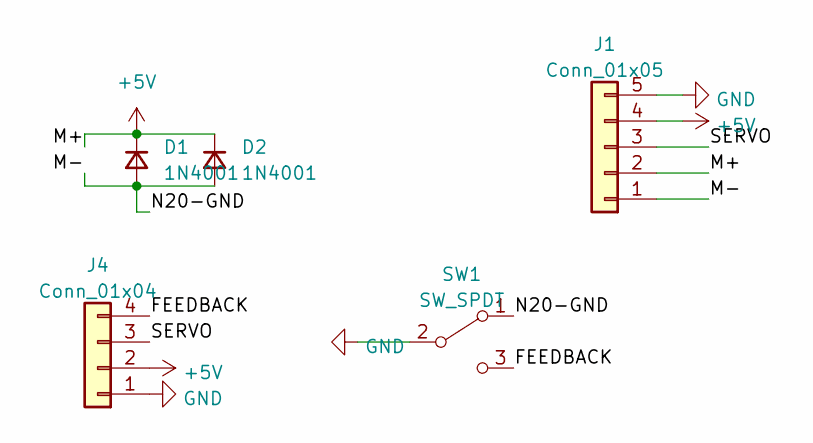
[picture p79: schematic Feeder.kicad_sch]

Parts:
D1: 1N4001; D_SMA-SMB_Universal_Handsoldering
D2: 1N4001; D_A-405_P7.62mm_Horizontal
J1: Conn_01x05; PinSocket_1x05_P2.54mm_Vertical_Clean_Locking
J4: Conn_01x04; PinSocket_1x04_P2.54mm_Vertical_Clean
SW1: SW_SPDT; Microswitch

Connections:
+5V: D1.1 (K), D2.1 (K), J1.2, J1.4, J4.2
/FEEDBACK: J4.4, SW1.3 (C)
/N20-GND: D1.2 (A), D2.2 (A), J1.1, SW1.1 (A)
/SERVO: J1.3, J4.3
GND: J1.5, J4.1, SW1.2 (B)

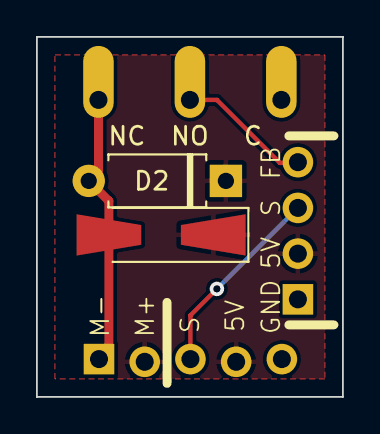
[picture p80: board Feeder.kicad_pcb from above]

Board: 2 copper layers, 17.0 x 20.0 mm, 5 parts (0 on the bottom side), 5 nets.

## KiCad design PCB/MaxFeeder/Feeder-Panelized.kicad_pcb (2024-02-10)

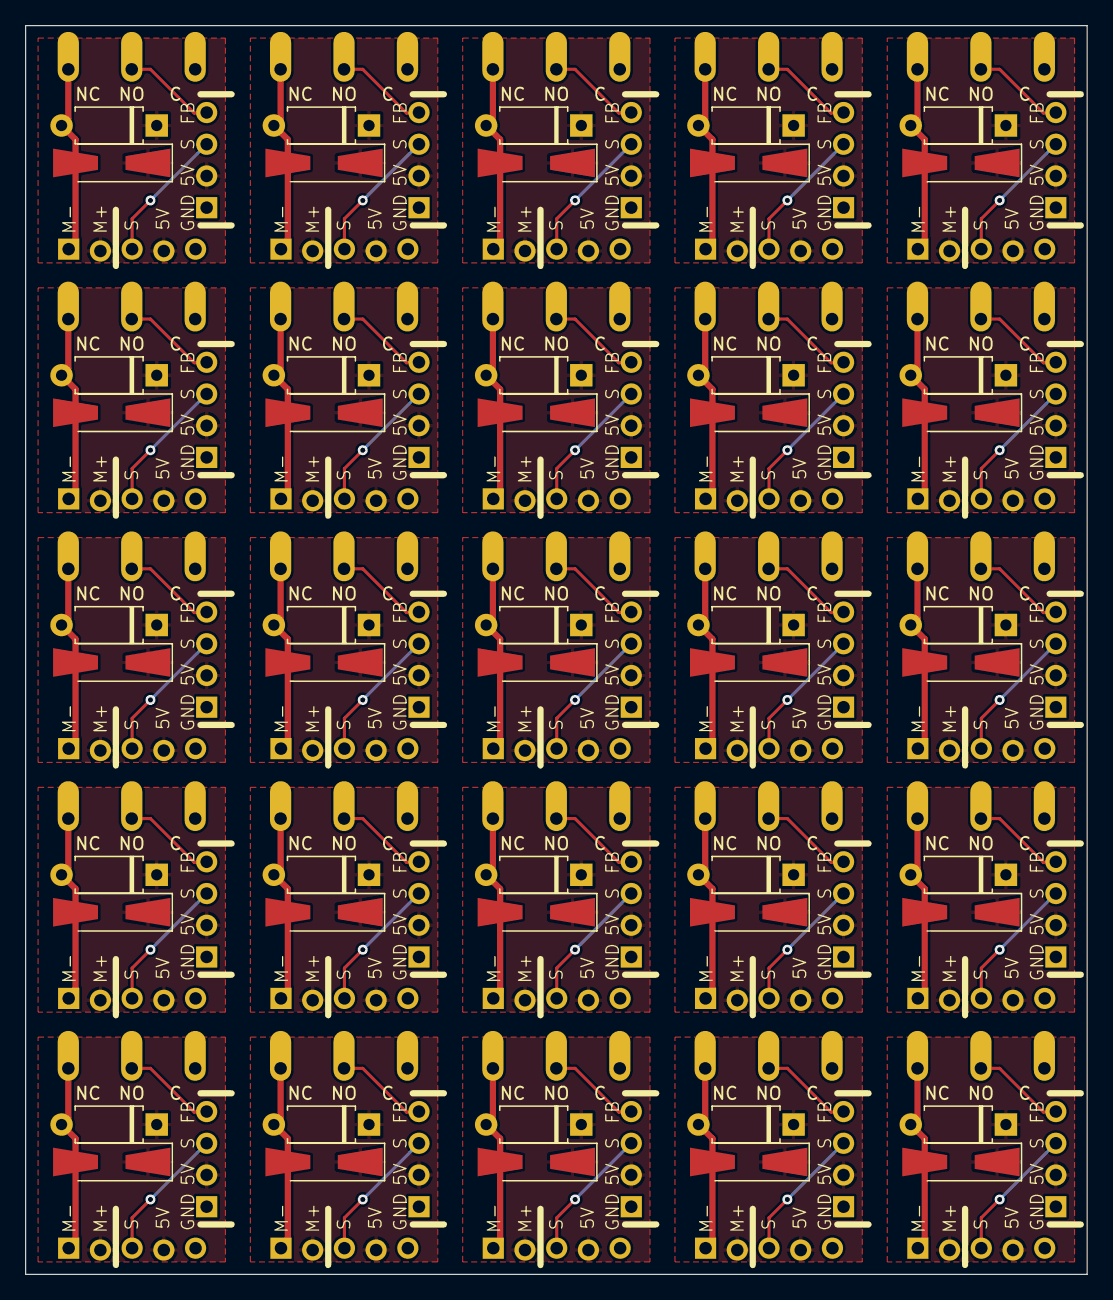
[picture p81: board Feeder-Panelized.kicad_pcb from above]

Board: 2 copper layers, 85.0 x 100.0 mm, 125 parts (0 on the bottom side), 5 nets.

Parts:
D1, D3, D5, D7, D9, D11, D13, D15, D17, D19, D21, D23, D25, D27, D29, D31, D33, D35, D37, D39, D41, D43, D45, D47, D49: 1N4001; D_SMA-SMB_Universal_Handsoldering
D2, D4, D6, D8, D10, D12, D14, D16, D18, D20, D22, D24, D26, D28, D30, D32, D34, D36, D38, D40, D42, D44, D46, D48, D50: 1N4001; D_A-405_P7.62mm_Horizontal
J1, J2, J3, J7, J9, J11, J13, J15, J17, J19, J21, J23, J25, J27, J29, J31, J33, J35, J37, J39, J41, J43, J45, J47, J49: Conn_01x05; PinSocket_1x05_P2.54mm_Vertical_Clean_Locking
J4, J5, J6, J8, J10, J12, J14, J16, J18, J20, J22, J24, J26, J28, J30, J32, J34, J36, J38, J40, J42, J44, J46, J48, J50: Conn_01x04; PinSocket_1x04_P2.54mm_Vertical_Clean
SW1, SW2, SW3, SW4, SW5, SW6, SW7, SW8, SW9, SW10, SW11, SW12, SW13, SW14, SW15, SW16, SW17, SW18, SW19, SW20, SW21, SW22, SW23, SW24, SW25: SW_SPDT; Microswitch

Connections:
+5V: D1.1 (K), D2.1 (K), D3.1 (K), D4.1 (K), D5.1 (K), D6.1 (K), D7.1 (K), D8.1 (K), D9.1 (K), D10.1 (K), D11.1 (K), D12.1 (K), D13.1 (K), D14.1 (K), D15.1 (K), D16.1 (K), D17.1 (K), D18.1 (K), D19.1 (K), D20.1 (K), D21.1 (K), D22.1 (K), D23.1 (K), D24.1 (K), D25.1 (K), D26.1 (K), D27.1 (K), D28.1 (K), D29.1 (K), D30.1 (K), D31.1 (K), D32.1 (K), D33.1 (K), D34.1 (K), D35.1 (K), D36.1 (K), D37.1 (K), D38.1 (K), D39.1 (K), D40.1 (K), D41.1 (K), D42.1 (K), D43.1 (K), D44.1 (K), D45.1 (K), D46.1 (K), D47.1 (K), D48.1 (K), D49.1 (K), D50.1 (K), J1.2, J1.4, J2.2, J2.4, J3.2, J3.4, J4.2, J5.2, J6.2, J7.2, J7.4, J8.2, J9.2, J9.4, J10.2, J11.2, J11.4, J12.2, J13.2, J13.4, J14.2, J15.2, J15.4, J16.2, J17.2, J17.4, J18.2, J19.2, J19.4, J20.2, J21.2, J21.4, J22.2, J23.2, J23.4, J24.2, J25.2, J25.4, J26.2, J27.2, J27.4, J28.2, J29.2, J29.4, J30.2, J31.2, J31.4, J32.2, J33.2, J33.4, J34.2, J35.2, J35.4, J36.2, J37.2, J37.4, J38.2, J39.2, J39.4, J40.2, J41.2, J41.4, J42.2, J43.2, J43.4, J44.2, J45.2, J45.4, J46.2, J47.2, J47.4, J48.2, J49.2, J49.4, J50.2
/FEEDBACK: J4.4, J5.4, J6.4, J8.4, J10.4, J12.4, J14.4, J16.4, J18.4, J20.4, J22.4, J24.4, J26.4, J28.4, J30.4, J32.4, J34.4, J36.4, J38.4, J40.4, J42.4, J44.4, J46.4, J48.4, J50.4, SW1.3 (C), SW2.3 (C), SW3.3 (C), SW4.3 (C), SW5.3 (C), SW6.3 (C), SW7.3 (C), SW8.3 (C), SW9.3 (C), SW10.3 (C), SW11.3 (C), SW12.3 (C), SW13.3 (C), SW14.3 (C), SW15.3 (C), SW16.3 (C), SW17.3 (C), SW18.3 (C), SW19.3 (C), SW20.3 (C), SW21.3 (C), SW22.3 (C), SW23.3 (C), SW24.3 (C), SW25.3 (C)
/N20-GND: D1.2 (A), D2.2 (A), D3.2 (A), D4.2 (A), D5.2 (A), D6.2 (A), D7.2 (A), D8.2 (A), D9.2 (A), D10.2 (A), D11.2 (A), D12.2 (A), D13.2 (A), D14.2 (A), D15.2 (A), D16.2 (A), D17.2 (A), D18.2 (A), D19.2 (A), D20.2 (A), D21.2 (A), D22.2 (A), D23.2 (A), D24.2 (A), D25.2 (A), D26.2 (A), D27.2 (A), D28.2 (A), D29.2 (A), D30.2 (A), D31.2 (A), D32.2 (A), D33.2 (A), D34.2 (A), D35.2 (A), D36.2 (A), D37.2 (A), D38.2 (A), D39.2 (A), D40.2 (A), D41.2 (A), D42.2 (A), D43.2 (A), D44.2 (A), D45.2 (A), D46.2 (A), D47.2 (A), D48.2 (A), D49.2 (A), D50.2 (A), J1.1, J2.1, J3.1, J7.1, J9.1, J11.1, J13.1, J15.1, J17.1, J19.1, J21.1, J23.1, J25.1, J27.1, J29.1, J31.1, J33.1, J35.1, J37.1, J39.1, J41.1, J43.1, J45.1, J47.1, J49.1, SW1.1 (A), SW2.1 (A), SW3.1 (A), SW4.1 (A), SW5.1 (A), SW6.1 (A), SW7.1 (A), SW8.1 (A), SW9.1 (A), SW10.1 (A), SW11.1 (A), SW12.1 (A), SW13.1 (A), SW14.1 (A), SW15.1 (A), SW16.1 (A), SW17.1 (A), SW18.1 (A), SW19.1 (A), SW20.1 (A), SW21.1 (A), SW22.1 (A), SW23.1 (A), SW24.1 (A), SW25.1 (A)
/SERVO: J1.3, J2.3, J3.3, J4.3, J5.3, J6.3, J7.3, J8.3, J9.3, J10.3, J11.3, J12.3, J13.3, J14.3, J15.3, J16.3, J17.3, J18.3, J19.3, J20.3, J21.3, J22.3, J23.3, J24.3, J25.3, J26.3, J27.3, J28.3, J29.3, J30.3, J31.3, J32.3, J33.3, J34.3, J35.3, J36.3, J37.3, J38.3, J39.3, J40.3, J41.3, J42.3, J43.3, J44.3, J45.3, J46.3, J47.3, J48.3, J49.3, J50.3
GND: J1.5, J2.5, J3.5, J4.1, J5.1, J6.1, J7.5, J8.1, J9.5, J10.1, J11.5, J12.1, J13.5, J14.1, J15.5, J16.1, J17.5, J18.1, J19.5, J20.1, J21.5, J22.1, J23.5, J24.1, J25.5, J26.1, J27.5, J28.1, J29.5, J30.1, J31.5, J32.1, J33.5, J34.1, J35.5, J36.1, J37.5, J38.1, J39.5, J40.1, J41.5, J42.1, J43.5, J44.1, J45.5, J46.1, J47.5, J48.1, J49.5, J50.1, SW1.2 (B), SW2.2 (B), SW3.2 (B), SW4.2 (B), SW5.2 (B), SW6.2 (B), SW7.2 (B), SW8.2 (B), SW9.2 (B), SW10.2 (B), SW11.2 (B), SW12.2 (B), SW13.2 (B), SW14.2 (B), SW15.2 (B), SW16.2 (B), SW17.2 (B), SW18.2 (B), SW19.2 (B), SW20.2 (B), SW21.2 (B), SW22.2 (B), SW23.2 (B), SW24.2 (B), SW25.2 (B)

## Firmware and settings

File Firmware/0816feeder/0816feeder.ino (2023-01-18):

/*
* Author: mgrl
* (c)2017-12-30
* 
* Modified by: Curly Tale Games
*
* This work is licensed under a Creative Commons Attribution-NonCommercial-ShareAlike 4.0 International License.
* http://creativecommons.org/licenses/by-nc-sa/4.0/
*
* current version: v0.3
*
* CHANGELOG:
* v0.2
*   - added support for sensor shield (experimental, no feedbackline supported)
* v0.3
*   - better checking for manual feed (enhanced reliability not to conflict with g-code issued feeds)
*   - improved setup sequence
*   - default angle for 2mm feeds corrected according to math
*
* v0.4
*  - added support for MaxFeederShield
*  - added support for software servo control using SoftServo library by Alex Gyver https://github.com/GyverLibs/SoftServo 
*    install through Tools > Manage Libraries
*  - added auto detach of servo motors so they don't burn up
*  - removed need to run M610 S1 command to enable since motors auto turn off
*/

#include "config.h"
#include "shield.h"

// ------------------  I N C  L I B R A R I E S ---------------
#include <HardwareSerial.h>
#include <EEPROMex.h>
#include "Feeder.h"

// ------------------  V A R  S E T U P -----------------------

// ------ Feeder
FeederClass feeders[NUMBER_OF_FEEDER];
enum eFeederEnabledState {
  DISABLED,
  ENABLED,
} feederEnabled=ENABLED; //enable feeders by default

// ------ Settings-Struct (saved in EEPROM)
struct sCommonSettings {

	//add further settings here

	char version[4];   // This is for detection if settings suit to struct, if not, eeprom is reset to defaults
#ifdef HAS_ANALOG_IN
	float adc_scaling_values[8][2];
#endif
};
sCommonSettings commonSettings_default = {

	//add further settings here

	CONFIG_VERSION,
 
#ifdef HAS_ANALOG_IN
	{
		{ANALOG_A0_SCALING_FACTOR,ANALOG_A0_OFFSET},
		{ANALOG_A1_SCALING_FACTOR,ANALOG_A1_OFFSET},
		{ANALOG_A2_SCALING_FACTOR,ANALOG_A2_OFFSET},
		{ANALOG_A3_SCALING_FACTOR,ANALOG_A3_OFFSET},
		{ANALOG_A4_SCALING_FACTOR,ANALOG_A4_OFFSET},
		{ANALOG_A5_SCALING_FACTOR,ANALOG_A5_OFFSET},
		{ANALOG_A6_SCALING_FACTOR,ANALOG_A6_OFFSET},
		{ANALOG_A7_SCALING_FACTOR,ANALOG_A7_OFFSET},
	},
#endif
};
sCommonSettings commonSettings;

// ------ ADC readout
unsigned long lastTimeADCread;
uint16_t adcRawValues[8];
float adcScaledValues[8];

// ------------------  U T I L I T I E S ---------------

// ------ Operate command on all feeder
enum eFeederCommands {
	cmdSetup,
	cmdUpdate,

	cmdEnable,
	cmdDisable,

	cmdOutputCurrentSettings,
	cmdInitializeFeederWithId,
	cmdFactoryReset,

};
void executeCommandOnAllFeeder(eFeederCommands command);
void executeCommandOnAllFeeder(eFeederCommands command) {
	for (uint8_t i=0;i<NUMBER_OF_FEEDER;i++) {
		switch(command) {
			case cmdSetup:
				feeders[i].setup();
			break;
			case cmdUpdate:
				feeders[i].update();
			break;
			case cmdEnable:
				feeders[i].enable();
			break;
			case cmdDisable:
				feeders[i].disable();
			break;
			case cmdOutputCurrentSettings:
				feeders[i].outputCurrentSettings();
			break;
			case cmdInitializeFeederWithId:
				feeders[i].initialize(i);
			break;
			case cmdFactoryReset:
				feeders[i].factoryReset();
			break;
			default:
				{}
			break;
		}
	}
}

#ifdef HAS_ANALOG_IN
void updateADCvalues() {

	for(uint8_t i=0; i<=7; i++) {
		adcRawValues[i]=analogRead(i);
		adcScaledValues[i]=(adcRawValues[i]*commonSettings.adc_scaling_values[i][0])+commonSettings.adc_scaling_values[i][1];
	}
}
#endif

void printCommonSettings() {

	//ADC-scaling values
#ifdef HAS_ANALOG_IN
	Serial.println("Analog Scaling Settings:");
	for(uint8_t i=0; i<=7; i++) {
		Serial.print("M");
		Serial.print(MCODE_SET_SCALING);
		Serial.print(" A");
		Serial.print(i);
		Serial.print(" S");
		Serial.print(commonSettings.adc_scaling_values[i][0]);
		Serial.print(" O");
		Serial.print(commonSettings.adc_scaling_values[i][1]);
		Serial.println();
	}
#endif
}

// ------------------  S E T U P -----------------------
void setup() {
	Serial.begin(SERIAL_BAUD);
	while (!Serial);
	Serial.println(F("Controller starting...")); Serial.flush();
	Serial.println(F("Here is some stuff saved in EEPROM. Paste in a textfile to backup these settings...")); Serial.flush();

	//feeder enable output
	//pinMode(FEEDER_ENABLE_PIN,OUTPUT);
	//digitalWrite(FEEDER_ENABLE_PIN,LOW);

	//power output init
	for(uint8_t i=0;i<NUMBER_OF_POWER_OUTPUT;i++) {
		pinMode(pwrOutputPinMap[i],OUTPUT);
		digitalWrite(pwrOutputPinMap[i],LOW);
	}
	
	// setup listener to serial stream
	setupGCodeProc();

	//initialize active feeders, this is giving them an valid ID
	//needs to be done before factory reset to have a valid ID (eeprom-settings location is derived off the ID)
	executeCommandOnAllFeeder(cmdInitializeFeederWithId);

	//load commonSettings from eeprom
	EEPROM.readBlock(EEPROM_COMMON_SETTINGS_ADDRESS_OFFSET, commonSettings);

	//factory reset on first start or version changing
	if(strcmp(commonSettings.version,CONFIG_VERSION) != 0) {
		Serial.println(F("First start/Config version changed"));

		//reset needed
		executeCommandOnAllFeeder(cmdFactoryReset);

		//update commonSettings in EEPROM to have no factory reset on next start
		EEPROM.writeBlock(EEPROM_COMMON_SETTINGS_ADDRESS_OFFSET, commonSettings_default);
	}

	//print all settings to console
	printCommonSettings();

	//setup feeder objects
  //digitalWrite(FEEDER_ENABLE_PIN, HIGH);  //power feeder first, because while setup feeder might retract.
	executeCommandOnAllFeeder(cmdSetup);	//setup everything first, then power on short. made it this way to prevent servos from driving to an undefined angle while being initialized
	delay(1000);		//have the last feeder's servo settled before disabling

  //**** keep the feeders enabled on startup ****
  executeCommandOnAllFeeder(cmdEnable);
  // executeCommandOnAllFeeder(cmdDisable); //while setup ran, the feeder were moved and remain in sIDLE-state -> it shall be disabled
	//digitalWrite(FEEDER_ENABLE_PIN, LOW);	//disable power afterwards
	
	//print all settings of every feeder to console
	executeCommandOnAllFeeder(cmdOutputCurrentSettings);

	//init adc-values
#ifdef HAS_ANALOG_IN
	updateADCvalues();
	lastTimeADCread=millis();
#endif

	Serial.println(F("Controller up and ready! Have fun."));
}



// ------------------  L O O P -----------------------

void loop() {

	//debouncedButton.update();

	// Process incoming serial data and perform callbacks
	listenToSerialStream();

	// Process servo control
	executeCommandOnAllFeeder(cmdUpdate);

	// Process ADC inputs
#ifdef HAS_ANALOG_IN
	if (millis() - lastTimeADCread >= ADC_READ_EVERY_MS) {
		lastTimeADCread=millis();

		updateADCvalues();
	}
#endif
}

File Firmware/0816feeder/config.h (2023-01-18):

#ifndef _CONFIG_h
#define _CONFIG_h
#include "arduino.h"


/*
*     DEBUG
*/
// prints some extra information via serial
// uncomment to disable in production
//#define DEBUG

/*
*  Select controller shield
*/
// defaults to the native shield, optional sensor shield can be selected
#define CONTROLLER_SHIELD SHIELD_MAX     //SHIELD_NATIVE or SHIELD_SENSOR or SHIELD_MAX
//change config_version, if change shield!


/*
*  EEPROM-Settings
*/
//change to something other unique if structure of data to be saved in eeprom changed (max 3 chars)
#define CONFIG_VERSION "aac"

/*
*  Serial
*/
#define SERIAL_BAUD 115200


/* -----------------------------------------------------------------
*  FEEDER CONFIG
*  -----------------------------------------------------------------
* default settings per feeder

// calculate angles: https://de.wikipedia.org/wiki/Schubkurbel, crankshift


	when setting these values, make sure, the values for
	FEEDER_DEFAULT_MOTOR_MIN_PULSEWIDTH and
	FEEDER_DEFAULT_MOTOR_MAX_PULSEWITH
	reflect the according position for servo being used

	when everything is setup right, the lever is in advanced position at servo-angle ~90 degree
	fully retracted is about ~20°


	| STATE RETRACTED, looking from the top
	|
	|   .
	|  /_\
	|   |			<- direction tape is advanced
	|   |
	|
	| -x-----		<- advancing lever, x falls into the hole of a tape and advances it.
	| -------
	| ----
	| ----
	| ----
	| ----
	| -------
	| -------
	| -------
	| -\\o\\-       <- piston / Pleuelstange
	|   \\\\\
	|    \\\\\
	|     \\\\\
	|      \\\\\
	|    O====o\\
	|    ^   \\\\\
	|    \_ servo-motor at FEEDER_DEFAULT_RETRACT_ANGLE (about 20°)

	| STATE FULL ADVANCED, looking from the top
	|
	|   .
	|  /_\
	|   |			<- direction tape is advanced
	|   |
	|
	| -x-----		<- advancing lever, x falls into the hole of a tape and advances it.
	| -------
	| ----
	| ----
	| ----
	| ----
	| -------
	| -------
	| -------
	| -||o||-       <- piston / Pleuelstange
	|  |||||
	|  |||||
	|  |||||
	|  |||||
	|  |||||
	|  ||o||
	|    :
	|    :			<- arm of servo motor fully extended
	|    :
	|    :
	|    0			<- servo-motor at FEEDER_DEFAULT_FULL_ADVANCED_ANGLE (about 90°)

*/
#define FEEDER_DEFAULT_FULL_ADVANCED_ANGLE  80				      // [°]  usually 90 (type: uint8_t)
#define FEEDER_DEFAULT_HALF_ADVANCED_ANGLE  40              // [°]  exact math would be 43.85. may need tweaking. only needed if advancing half pitch (for 0401 smds) (type: uint8_t)
#define FEEDER_DEFAULT_RETRACT_ANGLE  0				      // [°]  usually 20, chose 15 to be failsafe (type: uint8_t)
#define FEEDER_DEFAULT_FEED_LENGTH FEEDER_MECHANICAL_ADVANCE_LENGTH			// [mm] distance to be fed if no feedlength was given in a feed command
#define FEEDER_DEFAULT_TIME_TO_SETTLE  255			  // [ms] time the servo needs to travel from FEEDER_DEFAULT_FULL_ADVANCED_ANGLE to FEEDER_DEFAULT_RETRACT_ANGLE (type: uint8_t -> max 255ms)
/*
	 0° == ~ 544 µs	--> min, default 544 and seems it fits to the sg90 from tower pro
	90° ==          --> "middle"
   180° == ~2400 µs --> max, default 2400 and seems it fits to the sg90 from tower pro
	 --> SERVO.attach(PIN, 544, 2400);
*/
#define FEEDER_DEFAULT_MOTOR_MIN_PULSEWIDTH 544		// [µs] see motor specs or experiment at bit. Value set here should bring the servo to 0°
#define FEEDER_DEFAULT_MOTOR_MAX_PULSEWITH 2400		// [µs] see motor specs or experiment at bit. Value set here should bring the servo to 180°
#define FEEDER_DEFAULT_IGNORE_FEEDBACK 0			// 0: before feeding the feedback-signal is checked. if signal is as expected, the feeder advances tape and returns OK to host. otherwise an error is thrown.
													// 1: the feedback-signal is not checked, feeder advances tape and returns OK always


/* ----------------
  Analog Reading Config
*/
// ADC is polled regularly and scaled afterwards. When a command is issued, the pre-calculated values are sent to host immediately.
#define ADC_READ_EVERY_MS 20

// Scaling Factors to convert raw ADC value to real units.
#define ANALOG_A0_SCALING_FACTOR 0.1277			//preset for NXP vacuum sensor, formula pressure [kPa]=(ADCval/1023-0.92)/0.007652
#define ANALOG_A0_OFFSET -120.23
#define ANALOG_A1_SCALING_FACTOR 0.1277			//preset for NXP vacuum sensor, formula pressure [kPa]=(ADCval/1023-0.92)/0.007652
#define ANALOG_A1_OFFSET -120.23
#define ANALOG_A2_SCALING_FACTOR 1
#define ANALOG_A2_OFFSET 0
#define ANALOG_A3_SCALING_FACTOR 1
#define ANALOG_A3_OFFSET 0
#define ANALOG_A4_SCALING_FACTOR 1
#define ANALOG_A4_OFFSET 0
#define ANALOG_A5_SCALING_FACTOR 1
#define ANALOG_A5_OFFSET 0
#define ANALOG_A6_SCALING_FACTOR 1
#define ANALOG_A6_OFFSET 0
#define ANALOG_A7_SCALING_FACTOR 1
#define ANALOG_A7_OFFSET 0







// ------------------------------------------------------
//
//
//
//
//
//
//
// STOP
// do not edit stuff below this line...
//
//
//
//
//
//
//
//
// ------------------------------------------------------
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

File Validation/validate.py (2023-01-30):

# this script is for testing a 0816 style feeders
#  
# It requires Open PNP to be open and the camera settings to be adjusted
# so that the tape is white and the tape holes for the parts are below the threshold (black)
# 
# For more accurate measurements increase the size of the camera view in Open PNP
#
# download and install autohotkey and open the "Window Spy" application, you can use
# Window Spy to measure the pixel position on the screen, as well as the pixel color
# for the threshold

# adjust the screenshot region to be around the part you are measuring drift on
# measure distance in pixels between 4mm sprocket holes, mine was 65.8 pixels / mm


import pyautogui
import csv
import keyboard
import time
import serial
import numpy as np


# Set up serial communication
ser = serial.Serial(
    'COM3', 
    baudrate=115200, 
    bytesize=serial.EIGHTBITS,
    parity=serial.PARITY_NONE,
    stopbits=serial.STOPBITS_ONE,
    timeout=1,
    xonxoff=0,
    rtscts=0
    )

ser.setDTR(False)

# Wait for Arduino to initialize
time.sleep(10)

# Clear out unwanted startup serial data
ser.flushInput()
ser.setDTR(True)


# Take a screenshot of a 600x400 pixel section of the screen
def take_screenshot():
    screenshot = pyautogui.screenshot(region=(680, 330, 20, 140))
    return screenshot

# Convert the screenshot to a grayscale image
def convert_to_grayscale(screenshot):
    gray_image = screenshot.convert("L")
    return gray_image

# Find the coordinates of the top and bottom of the part rectangle
def find_black_pixel_height(gray_image):

    height = gray_image.size[1]
    # x = 10
    threshold = 200
    columns = 10

    # Initialize a counter for the height of black pixels


    black_height = []
    top = []
    bottom = []
    center = []

    # Iterate over 10 columns of pixels to surpress noise or other artifacts
    for x in range(columns):
        black_height.append(0)
        top.append(-1)
        bottom.append(-1)
        center.append(-1)
        # Iterate over each pixel in the image
        for y in range(height):
            # Get the pixel value at (x, y)
            pixel = gray_image.getpixel((x, y))
            # If the pixel is below threshold (black), increment the counter
            if pixel < threshold:
                if top[x] == -1:
                    top[x] = y
                black_height[x] += 1
                bottom[x] = y
        center[x] = top[x] + (black_height[x] / 2)

    # print([top, bottom, black_height, center])
    print([np.average(top), np.average(bottom), np.average(black_height), np.average(center)])
    return [np.average(top), np.average(bottom), np.average(black_height), np.average(center)]
    # return [top, bottom, black_height, center]
    

# Calculate the height of the black rectangle in pixels
def calculate_rectangle_height(top, bottom):
    height = bottom - top
    return height

# Log the result to a CSV file
def log_result(top, bottom, height, center):
    with open("results.csv", "a", newline="") as csv_file:
        writer = csv.writer(csv_file)
        log_data =[top, bottom, height, center]
        writer.writerow(log_data)

# Send a message over serial
def send_message(message):
    # ser.write(message.encode())
    ser.write(message)

# Main loop
while True:
    # Check if the space key has been pressed
    if keyboard.is_pressed("space"):
        break

    # Take a screenshot of the screen
    screenshot = take_screenshot()

    # Convert the screenshot to a grayscale image
    gray_image = convert_to_grayscale(screenshot)

    # Find the coordinates of the black rectangle in the grayscale image
    top, bottom, height, center = find_black_pixel_height(gray_image)

    # Log the result to a CSV file
    log_result(top, bottom, height, center)

    # Sleep for 4 seconds
    time.sleep(4)

    # Send a message over serial
    # send_message("M600 N0 F4" + '\r\n')
    ser.write(b'M600 N0 F4\r\n')

    # Sleep for 4 seconds
    time.sleep(4)

# Close the serial connection
ser.close()

print("Script terminated.")

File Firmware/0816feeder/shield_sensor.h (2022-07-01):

/*
 * capabilities
*/
#define NUMBER_OF_FEEDER 48
#define NO_ENABLE_PIN
#define NO_FEEDBACKLINES
#define NO_ANALOG_IN
#define NO_POWER_OUTPUTS
#define SOFT_SERVO_NUMBER 0

/*
* feederPinMap: Map IO-pins to specific feeder. First feeder is at index 0 (N0). Last feeder is NUMBER_OF_FEEDER-1
*/
const static uint8_t feederPinMap[NUMBER_OF_FEEDER] = {
  7,6,5,4,    // Feeder N0...N3
  22,23,24,25,
  26,27,28,29,
  30,31,32,33,
  34,35,36,37,
  38,39,40,41,
  42,43,44,45,
  46,47,48,49,
  A0,A1,A2,A3,
  A4,A5,A6,A7,
  A8,A9,A10,A11,
  A12,A13,A14,A15,
};


/*
* feederFeedbackPinMap: Map IO-pins to feedback-line to specific feeder. First feeder is at index 0 (N0). Last feeder is NUMBER_OF_FEEDER-1
* Feedback-line is usually connected to a microswitch to determine whether the feeder has a tape loaded and cover tape is tensioned
*
* to disable feedback-functionality completely at compile-time set pin to -1
*/
const static int8_t feederFeedbackPinMap[NUMBER_OF_FEEDER] = {
  -1,-1,-1,-1,
  -1,-1,-1,-1,
  -1,-1,-1,-1,
  -1,-1,-1,-1,
  -1,-1,-1,-1,
  -1,-1,-1,-1,
  -1,-1,-1,-1,
  -1,-1,-1,-1,
  -1,-1,-1,-1,
  -1,-1,-1,-1,
  -1,-1,-1,-1,
  -1,-1,-1,-1,
};

/*
* FEEDER_ENABLE_PIN
* IO-pin with a mosfet to switch power to all feeder on/off
*
* TODO: feature can't be disabled until today
*/
#define FEEDER_ENABLE_PIN 8



/* ----------------
  MOSFET power output pinmap

  on pcb 4 output are prepared. output 1 is at index 0 in pwrOutputPinMap
*/

#define NUMBER_OF_POWER_OUTPUT 0
const static uint8_t pwrOutputPinMap[NUMBER_OF_POWER_OUTPUT] = {};

const static uint8_t softwareServoPins[SOFT_SERVO_NUMBER] = {};

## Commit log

2022-05-19 hello world!
    [MAXFeederShield.kicad_pcb, MAXFeederShield.kicad_sch]
2022-07-01 Redesigned shield PCB, as well as adapter PCB, modified 0816 feeder firmware
    [Feeder-Panelized-B_Cu.gbr, Feeder-Panelized-B_Mask.gbr, Feeder-Panelized-B_Paste.gbr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]
2022-07-12 tweaked pad size on PCB and added 3d files for 8mm feeder
    [1mm-20deg-7t-m3.3mf, 1mm-20deg-8t-key.3mf, FeederBase.3mf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]
2022-07-12 fixed 3d model, updated docs
    [1mm-20deg-7t-m3.3mf, 1mm-20deg-8t-key.3mf, TapeGearBase.3mf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]
2022-07-14 added correct 3d gear part, added pictures, and fixed typo
    [TapeGearBase.3mf, TapeMotorBase.3mf]
2022-07-17 updated feeder design and documentation
    [1mm-20deg-7t-m3.3mf, 1mm-20deg-7t-m3.stl, 1mm-20deg-8t-key.3mf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]
2022-07-19 added 0.1mm to gear axle diameter thinned QR mounting point to snap on, and added links to docs
    [1mm-20deg-7t-m3.stl, 1mm-20deg-8t-key.stl, FeederBase.stl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]
2022-11-20 removed need for M610 S1 command, auto detach servos
2023-01-18 updated 3d files, updated docs, added validation script
    [1mm-20deg-7t-m3-0.4mm-nozzle.stl, 1mm-20deg-7t-m3.stl, 1mm-20deg-8t-key-axel-0.4mm-nozzle.stl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]
2023-01-18 added bracket step file
    [MaxFeederShieldMount.step]
2023-01-30 Added more clearance for thicker 8mm paper tape, and adjusted leaf spring to also work better with thinner plastic tapes
    [FeederBase.stl, FeederCover.stl, LeafSpingHeavy.stl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]
2023-02-02 added updated documentation - updated max feeder shield bracket
    [MaxFeederShield2020.stl, MaxFeederShieldBase.stl, MaxFeederShieldMount.3mf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]
2023-02-04 fixed docs, updated leaf spring
    [LeafSpingHeavy.stl, _plate2.3mf]
2023-02-05 updated front page readme, added error regex
    [MaxFeederShieldMount.3mf]
2023-03-28 launched online store
    [_plate1-0.4mm-nozzle.3mf]
2023-04-16 added beta 12mm feeders and added pro tip to motor gears
    [1mm-20deg-7t-m3-0.4mm-nozzle.stl, 1mm-20deg-8t-key-axel-0.4mm-nozzle.stl, FeederBase-12mm.stl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]
2023-11-05 Added PCB poker tip, added 8-24mm feeder widths, updated docs, cleaned up repo
    [1mm-20deg-7t-m3-0.4mm-nozzle-0.05mm.stl, 1mm-20deg-7t-m3-0.4mm-nozzle-0.10mm.stl, 1mm-20deg-7t-m3-0.4mm-nozzle-0.15mm.stl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]
2023-11-05 added photo of pcb poker tips
2023-11-07 forgot to include the washer in the plate, updated the 24mm base leaf spring to have more contact with bed
    [FeederBase.stl, _max-feeder-24mm-plate.3mf, _max-feeder-small-parts-plate.3mf]
2023-11-16 added support for DIN rail mounted feeders for liteplacer. Updated leaf spring for more reliable printing
    [DIN-FeederBase.stl, DIN-FeederCover.stl, FeederBase.stl]
2023-12-03 added 2040 max feeder version, fixed hole diameter in base, thicker leaf spring to easier printing
    [2040-FeederBase.stl, 2040-FeederCover.stl, DIN-FeederBase.stl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]
2024-02-10 removed unique part number silk screen on diodes
    [Feeder-Panelized-B_Cu.gbr, Feeder-Panelized-B_Mask.gbr, Feeder-Panelized-B_Paste.gbr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]
